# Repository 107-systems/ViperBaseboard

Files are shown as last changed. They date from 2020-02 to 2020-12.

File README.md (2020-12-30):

ViperBaseboard
==============

<p align="center">
  
</p>

This repository contains the requirements and the hardware design for MKR Vidor 4000 based Viper quadcopter.

## Quadcopter renderings
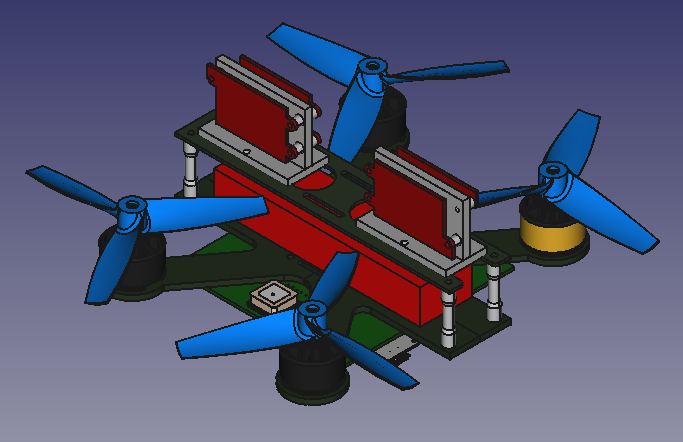
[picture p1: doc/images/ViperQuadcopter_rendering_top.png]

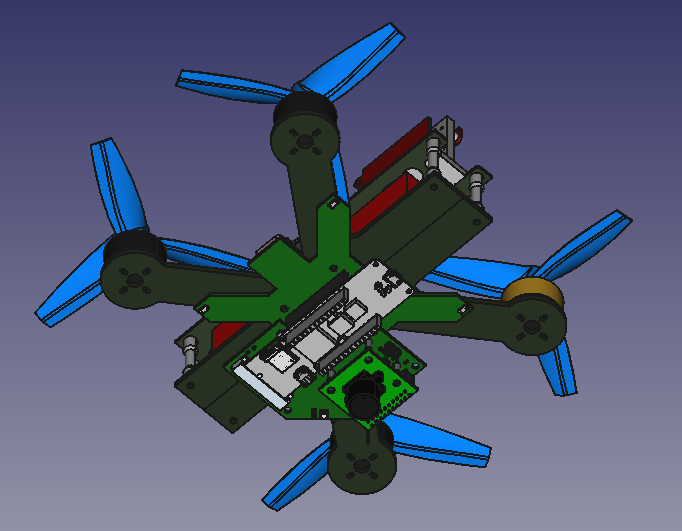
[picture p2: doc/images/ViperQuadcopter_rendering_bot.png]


## PCB renderings
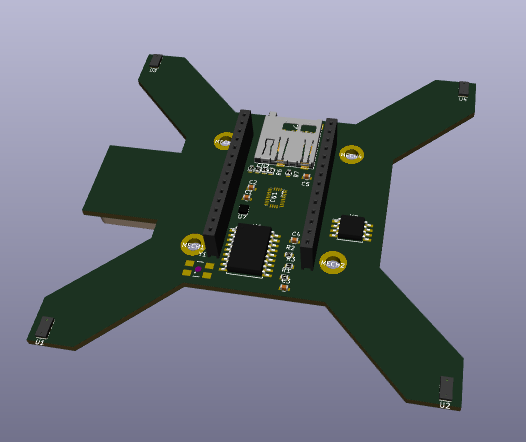
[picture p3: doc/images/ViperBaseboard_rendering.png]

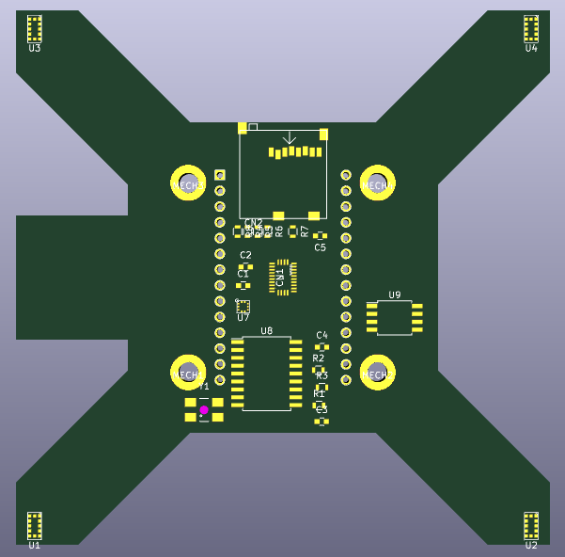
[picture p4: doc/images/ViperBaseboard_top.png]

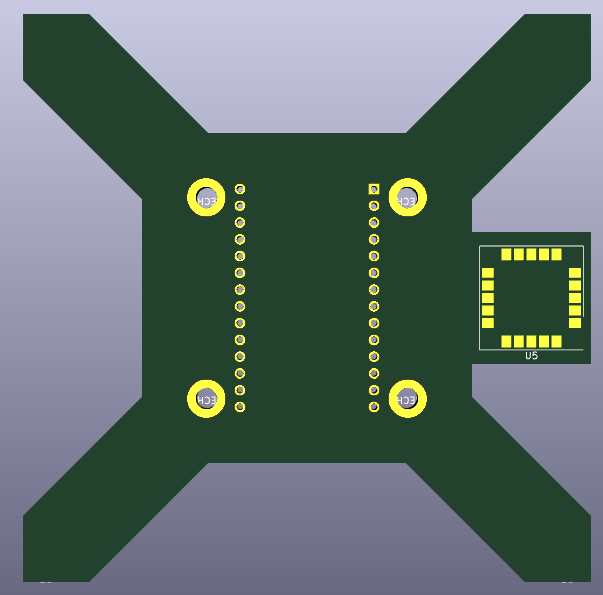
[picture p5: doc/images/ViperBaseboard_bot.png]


The **Viper Baseboard** serves as an adapter board between an Arduino MKR Vidor 4000 and various sensors and actuators in order to implement a flight controller for a quadcopter UAV.

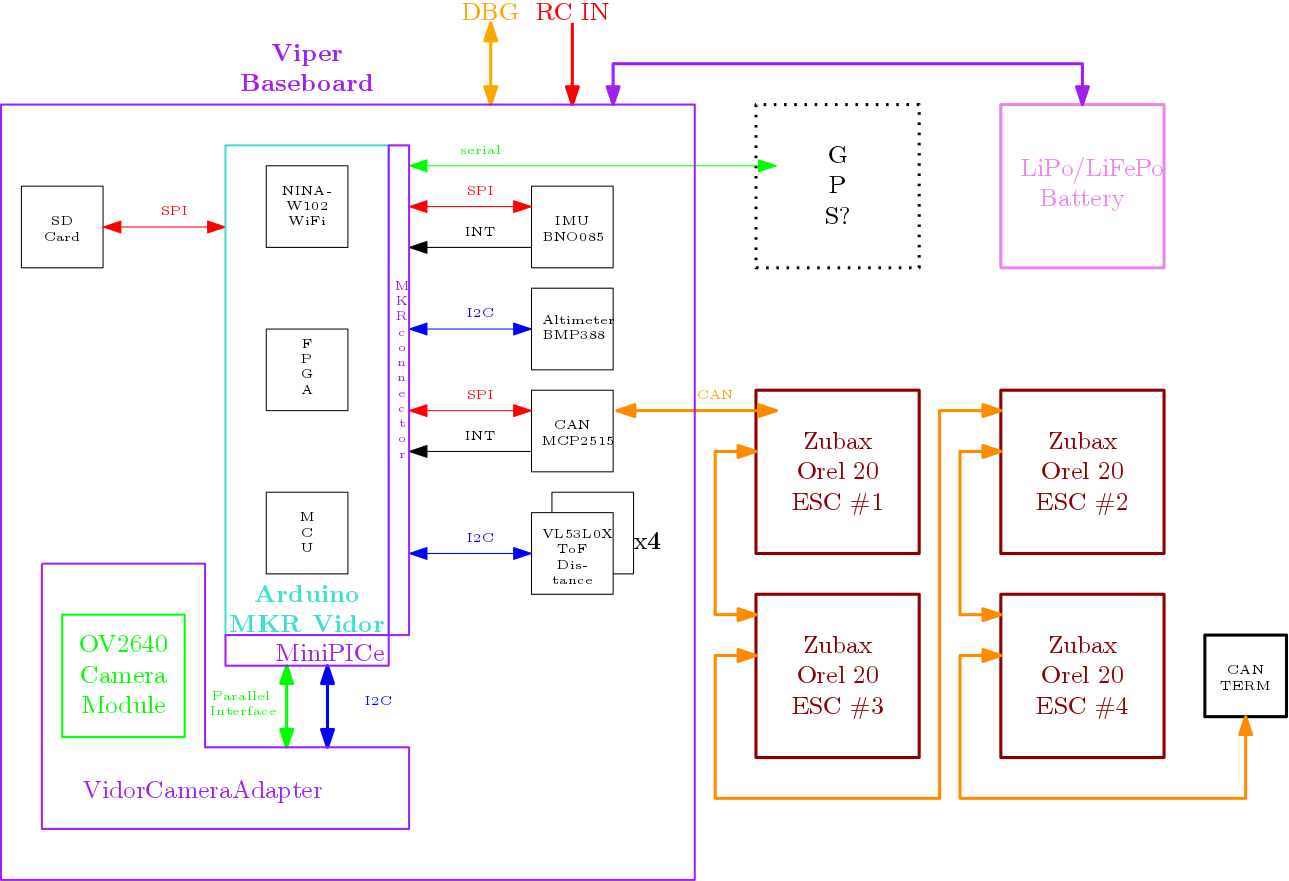
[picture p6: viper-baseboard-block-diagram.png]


The block diagramm has been created using [Ipe](http://ipe.otfried.org/) which can be installed via `sudo apt-get install ipe texlive-full` or `sudo apt-get install ipe texlive-base texlive-latex-recommended` for minimal installation).

## Requirements
### Functional Requirements
#### Rotational/Translational Stabilisation
The quadcopter should be able to stabilise itself against external disturbances concerning its orientation and position with respect to a given setpoint. For determining the current orientation of the quadcopter a suitable Inertial Measurement Unit (IMU) with a suitable sensor fusion algorithm shall be used. For determining translational stabilisation a optical flow sensor consisting of a downward facing camera in combination with a suitable optical flow sensor algorithm shall be used.

#### Vertical (Height) Stabilisation
The quadcopter should be able to hold a set distance over ground. In close proximity to the ground VL53L0X ToF sensors are used to  determine the distance between ground and quadcopter and prevent an accidential crash. When the distance between quadcopter and ground exceeds the maximum measurement range of the ground sensors the height will be controlled using a digital altimeter such as the BMP388.

#### WiFi based Control/Configuration
The quadcopter shall provide a WiFi access point to which a WiFi capable device can connect. Once a WiFi connection is established the quadcopter can be controlled via commands exchanged between quadcopter and device via a network socket. A webserver will run on the quadcopter which allows the user to configure and tweak certain aspects of the quadcopter configuration (e.g. control parameters) or read out quadcopter status.

#### Automonous Landing
The quadcopter should be able to land without user control. Three VL53L0X ToF sensors arranged in a triangle are used to determine the distance between ground and quadcopter and also perform an estimation of the grounds surface.

#### FPV (First-Person-View) Control
The image stream of a forward facing camera (a MIPI connector intented for use with the Omnivision OV5647 camera is available on the MKR VIDOR 4000 board) should be suitably encoded (in the FPGA) and transmitted via WiFi module in such way that a user can be view the image stream e.g. on a mobile phone which allows a FPV control of the quadcopter.\
It should be posible to switch the FPV from forward facing camera to ground facing camera and back. Then the user can choose which camera fits best his needs.

#### SD Card Storage
There should be a socket for a SD card on the baseboard. The flight controller then can log information like position or altitude or store video clips of the cameras or do image generation like map creation with the ground facing camera.

### Sensors
#### VL53L0X
The VL53L0X ToF Sensor allows a measurement range of up to 2 m with a resolution of 1 mm.\
**Attention:** all VL53L0X come up with the same I2C address. So we need additional circuitry to disable them with the XSHUT pin und give them individual addresses one after another.
#### BMP388
The BMP388 is a precision barometric pressure sensor wich relative accuracy of 8 Pascals, which translates to about ± 0.5 meter of altitude.
#### BNO085
The BNO085 contains 3 axis accelerometers, gyroscopes and magnetometers incl. onboard-algorithms for sensor fusion.
#### CD-PA1010D (Optional)
The [CD-PA1010D](doc/datasheet/Sensor-GPS-CD-PA1010D-v-0-3.pdf) is global positioning sensor supporting GPS, GLONASS, GALILEO, QZSS which can be interfaced both via UART and I2C.

### Actuators
#### Zubax Orel 20 ESCs
[Zubax Orel 20](https://kb.zubax.com/display/MAINKB/Zubax+Orel+20) are used as ESC (Electronic Speed Controllers) and controlled via [UAVCAN](https://uavcan.org).

### Electrical Requirements

* **Input Voltage**: 9 - 18.5 V (same as the Zubax Orel 20).
* **Input Protection**: Input voltage should be protected by a TVS diode against voltage spikes from the motors.
There is no fuse because the motor drivers can draw excessive currents. Then a fuse is useless because it should have a very high current rating and then it can'tprotect very much. Additionally the fuse would add additional weight and empose a risk of failure during flight.

#### Power planes and distribution
* **Input Voltage**: to motor drivers and input for voltage regulators, current: 20 to 30 A.
* **5V**:
Input for Arduino because the Arduino doesn't like to be directly fed with 3.3V.
generated on by a switching regulator.
Current: 500 mA + Current for 3.3V devices
* **3.3V**:
for sensors and camera module
generated by the onboard regulator of the Arduino
Current: up to 100 mA, should be OK for the onboard regulator

#### Connectors (mechanical and pinout)
##### Battery / Input
##### CAN
The Zubax Orel 20 ESCs utilize the [JST GH](http://www.jst-mfg.com/product/detail_e.php?series=105) connectors with a pitch of 1.25 mm.

| **Pin** | **Signal** |
|:---:|:---:|
| 1 | VCC |
| 2 | CAN_H |
| 3 | CAN_L |
| 4 | GND |

#### Connections of Arduino MKR Vidor 4000

* **MKR connector** (2.54 mm pinheader, 28 pins)
  * I2C
  * CAN over SPI (like on MKRCANShield)
  * 5V input, 3.3V output
  * RC_IN (for additional remote control receiver)

| **Pin** | **Pin Name** | **Signal** | **Description** |
|:---:|:---:|:---:|:---:|
| 1 | AREF | not connected | |
| 2 | DAC0/A0 | | |
| 3 | A1 | | |
| 4 | A2 | | |
| 5 | A3 | | |
| 6 | A4 | | |
| 7 | A5 | | |
| 8 | A6 | | |
| 9 | D0 | RC_IN | remote receiver input |
| 10 | D1 | | |
| 11 | D2 | | |
| 12 | D3 | MCP2515_CS | like MKRCANShield |
| 13 | D4 | SD_CS | like MKR SD PROTO SHIELD |
| 14 | D5 | | |
| 15 | D6 | | |
| 16 | D7 | MCP2515_INT | like MKRCANShield |
| 17 | D8/MOSI | MOSI | MCP2515 |
| 18 | D9/SCK | SCK | MCP2515 |
| 19 | D10/MISO | MISO | MCP2515 |
| 20 | D11/SDA | SDA | I2C for sensors |
| 21 | D12/SCL | SCL | I2C for sensors |
| 22 | D13/RX | GPS_RX | communication with gps module  |
| 23 | D14/TX | GPS_TX | communication with gps module  |
| 24 | RESET | not connected | |
| 25 | GND | GND | |
| 26 | 3V3 | 3V3-rail | supply voltage for sensors ... |
| 27 | VIN | 5V | input from voltage regulator |
| 28 | 5V | not connected | |

* **USB**: Programming and debugging
* **I2C**: Not used, redundant to MKR connector
* **LiPo**: not used, not suitable
* **MicroHDMI**: not used
* **MiPi Camera Connector**: reserved for front facing camera
* **MiniPCIe Connector**: Connection to OV2640 camera module serving as optical flow sensor. Using VidorCameraAdapter.

### Mechanical Requirements

* **Mounting**: No enclosure planed.
* **Mounting**: There should be mounting holes to mount the baseboard on the [Armattan F1-4B 3MM frame](https://www.armattanquads.com/f1-4b-3mm/)
* **Weight**: The weight should be as low as possible to get better flight performance
* **Cameras**: One camera is mounted on the botom and is facing to the ground. There is an option for a second camera facing forward.

### Environmental Requirements

* **Temperature**: Commercial temperature range should be OK. But parts with industrial range are preferred because of higher reliability.
* **Shock/Vibration**: Care should be taken because of higher vibration on copter therefore no high parts like electrolytic capacitors

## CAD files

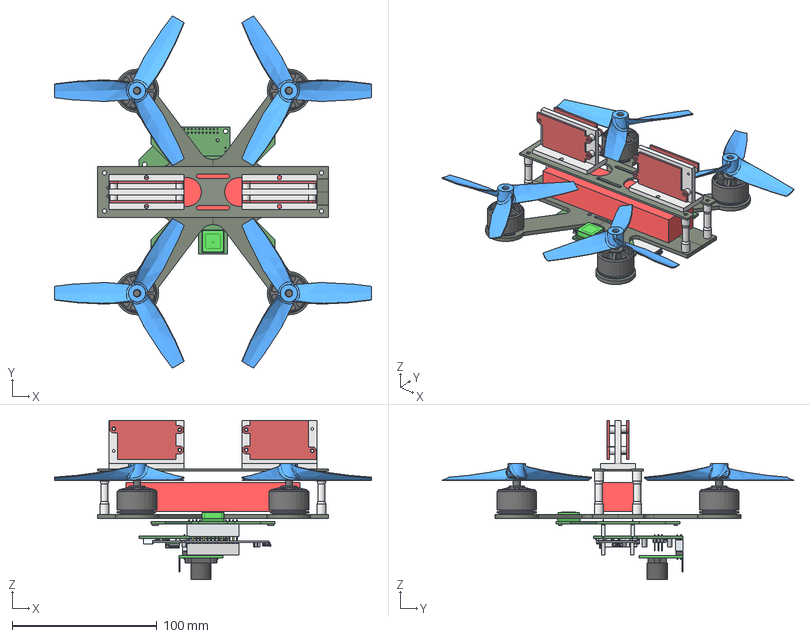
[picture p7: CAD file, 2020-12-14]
ViperQuadcopter.FCStd
219.3 x 243.4 x 110.2 mm
Frame_175mm
vidor
PCB
Package
X2
Pads
LILY_Antenna_Rev_D
685119248223_PIN
685119248223_PIN001
685119248223_PIN002
685119248223_PIN003
685119248223_PIN004
685119248223_PIN005
685119248223_PIN006
685119248223_PIN007
685119248223_PIN008
685119248223_INF
685119248223_SHIELDING
Shielding
Insulator
Pin
Pin001
Pin002
Pin003
Pin004
_T1SSW-114-03-G-S
_P2SSW-114-03-G-S
_T1SSW-114-03-G-S001
_P2SSW-114-03-G-S001
PCB002
pin
connector_frame
camera
battery
top plate
distance bolt
distance bolt001
distance bolt002
distance bolt003
zubax_orel001
zubax_orel
holder
zubax_orel002
zubax_orel003
holder001
T345V1_PROP
T345V1_PROP (Mirror #3)
T345V1_PROP (Mirror #7)
T345V1_PROP (Mirror #5)
F60 2200KV v2 (Mirror #4)
F60 2200KV v2
F60 2200KV v2 (Mirror #8)
F60 2200KV v2 (Mirror #6)

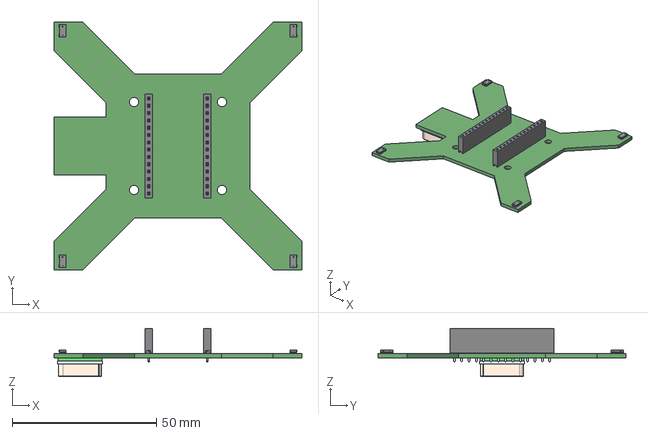
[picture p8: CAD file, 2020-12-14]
ViperBaseboard.step
86.0 x 86.0 x 16.7 mm

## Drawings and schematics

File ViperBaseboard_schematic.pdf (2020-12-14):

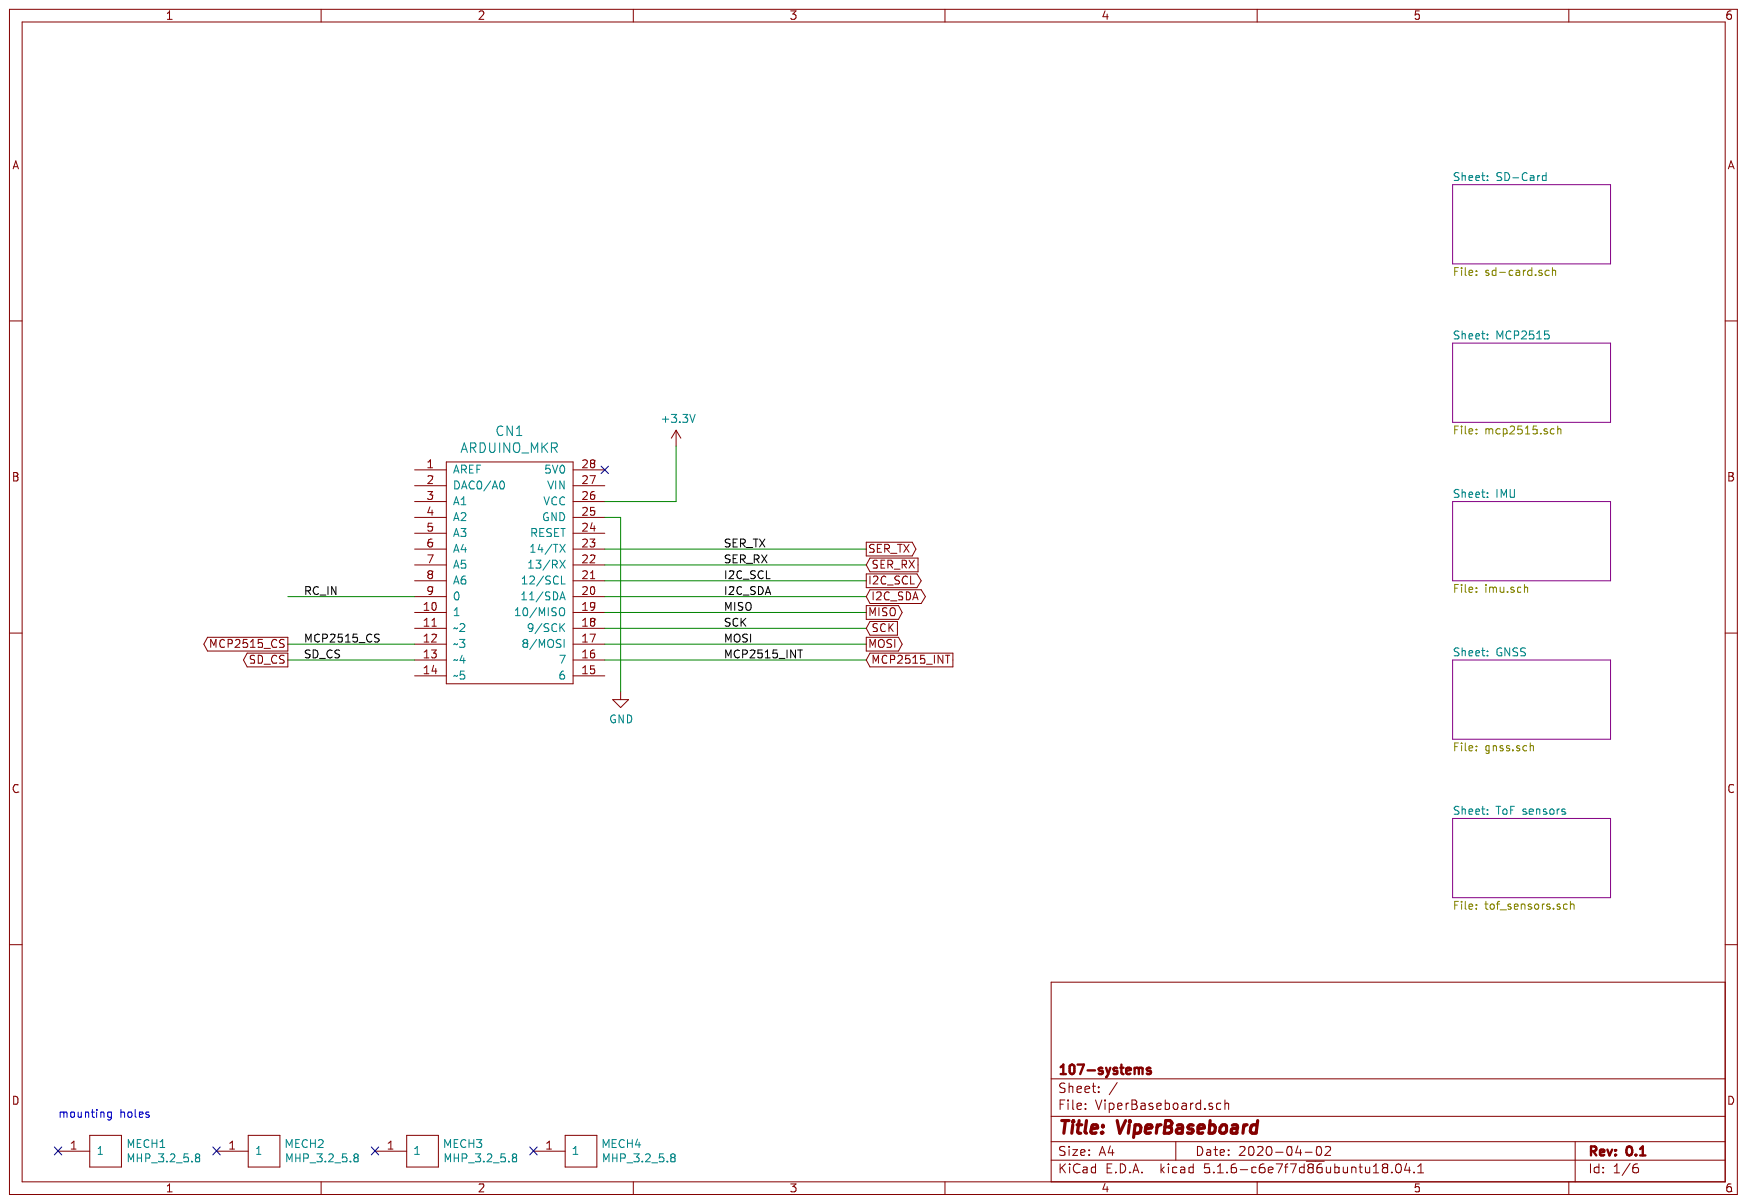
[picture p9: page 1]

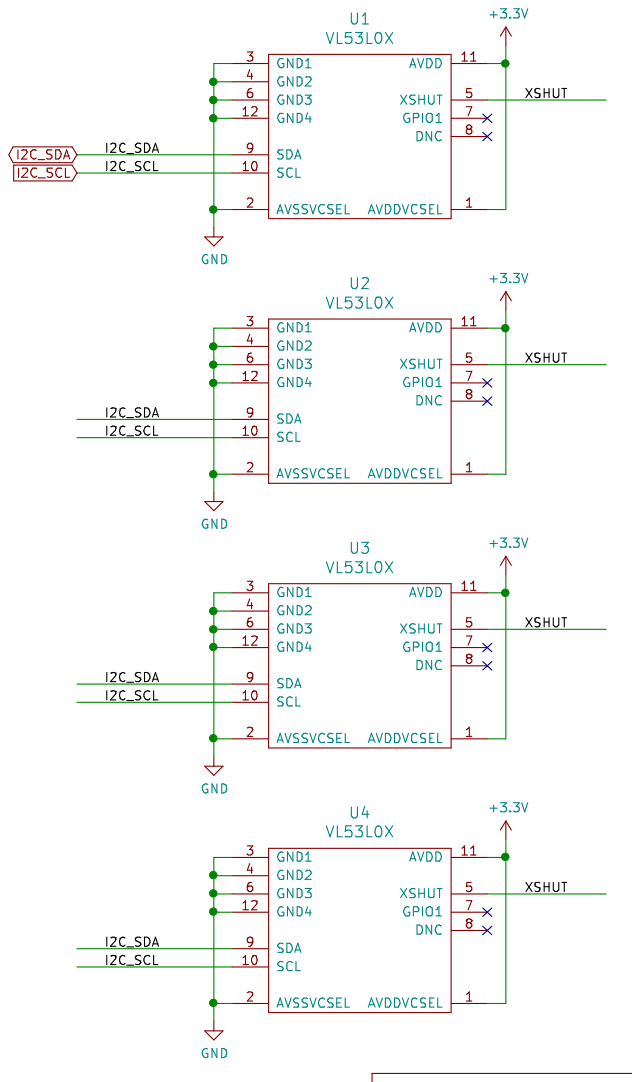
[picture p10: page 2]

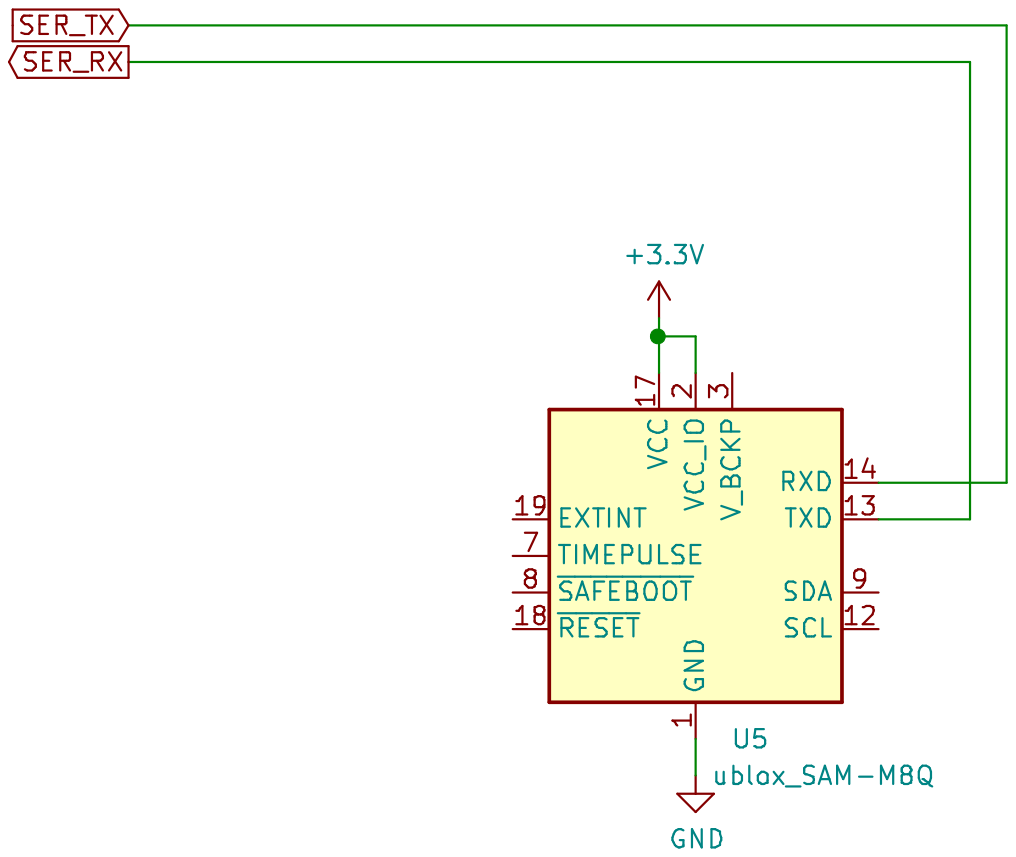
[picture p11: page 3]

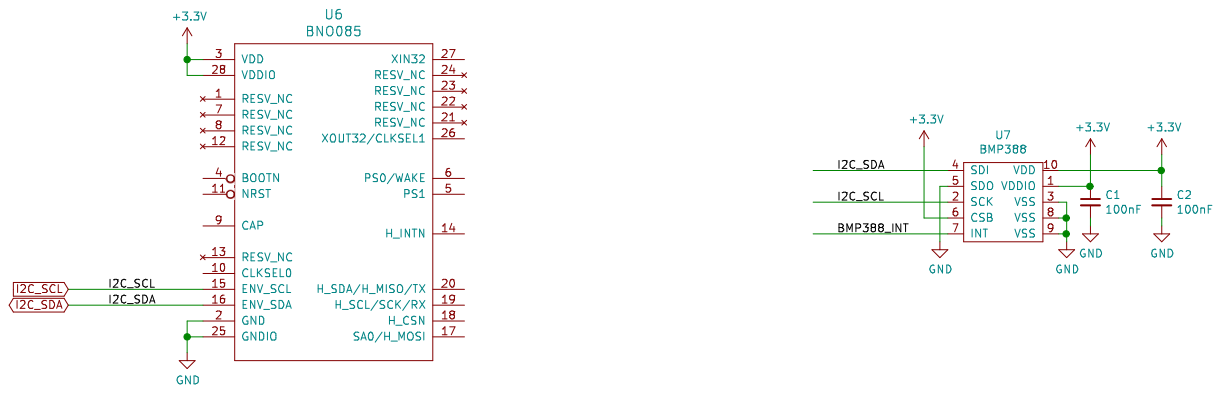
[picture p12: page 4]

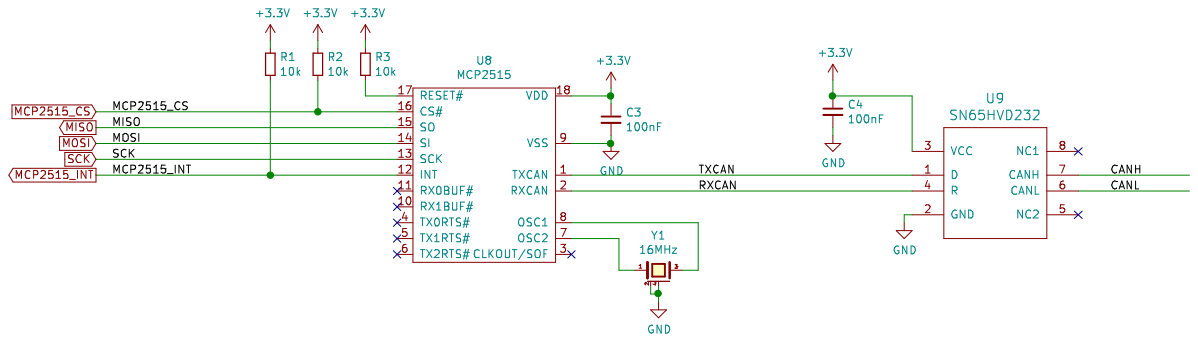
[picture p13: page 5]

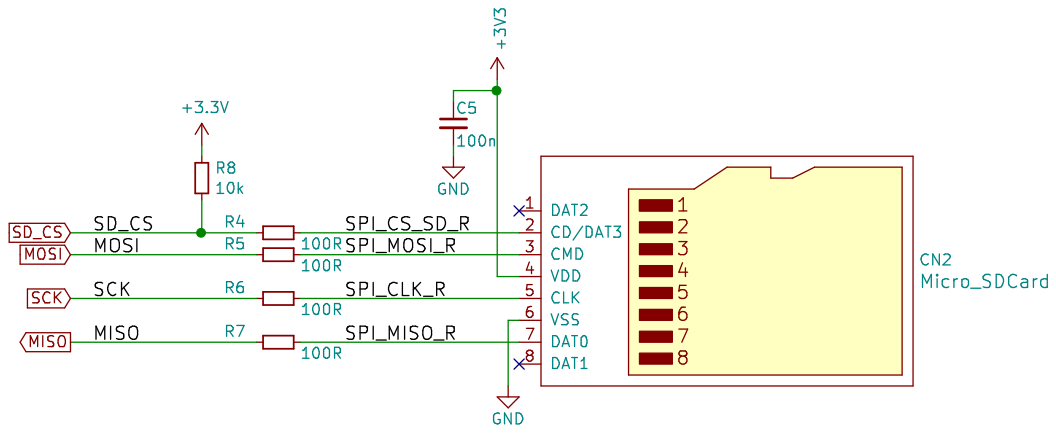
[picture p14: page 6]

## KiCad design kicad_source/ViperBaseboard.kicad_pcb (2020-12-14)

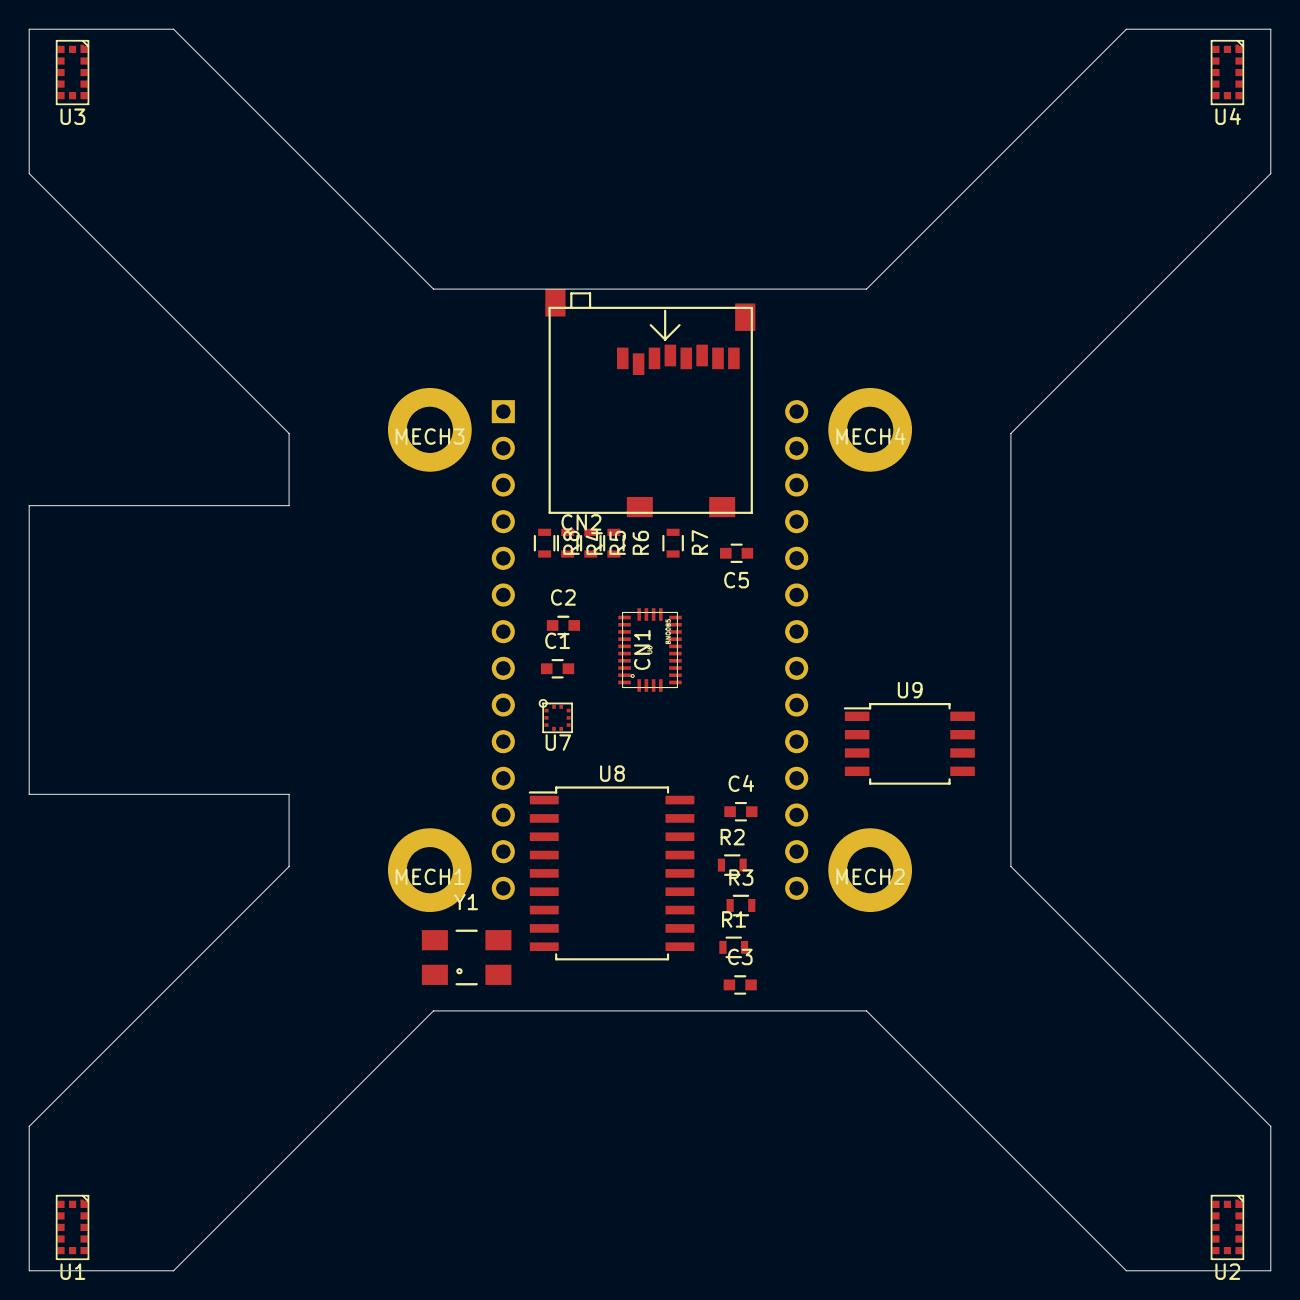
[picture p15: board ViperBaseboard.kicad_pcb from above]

Board: 2 copper layers, 86.0 x 86.0 mm, 29 parts (1 on the bottom side), 22 nets, no tracks yet.

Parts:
C1, C2, C3, C4: 100nF; C_0603
C5: 100n; C_0603
CN1: ARDUINO_MKR; ARDUINO_MKR_BASEBOARD
CN2: Micro_SDCard; WE_693071010811
MECH1, MECH2, MECH3, MECH4: MHP_3.2_5.8
R1, R2, R3, R8: 10k; R_0603
R4, R5, R6, R7: 100R; R_0603
U1, U2, U3, U4: VL53L0X
U5: ublox_SAM-M8Q
U6: BNO085; LGA-28-5832
U7: BMP388
U8: MCP2515; SOIC-18_7.5x11.6mm_Pitch1.27mm
U9: SN65HVD232; SOIJ-8_5.3x5.3mm_Pitch1.27mm
Y1: 16MHz; Crystal_SMD_0603_4Pads

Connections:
+3V3: C1.1, C2.1, C3.1, C4.1, C5.1, CN1.26, CN2.4, R1.1, R2.1, R3.1, R8.1, U1.1, U1.11, U2.1, U2.11, U3.1, U3.11, U4.1, U4.11, U5.2, U5.17, U6.3, U6.28, U7.1, U7.6, U7.10, U8.18, U9.3
/MCP2515/RXCAN: U8.2, U9.4
/MCP2515/TXCAN: U8.1, U9.1
/SD-Card/SPI_CLK_R: CN2.5, R6.1
/SD-Card/SPI_CS_SD_R: CN2.2, R4.1
/SD-Card/SPI_MISO_R: CN2.7, R7.1
/SD-Card/SPI_MOSI_R: CN2.3, R5.1
/ToF sensors/XSHUT: U1.5, U2.5, U3.5, U4.5
GND: C1.2, C2.2, C3.2, C4.2, C5.2, CN1.25, CN2.6, U1.2, U1.3, U1.4, U1.6, U1.12, U2.2, U2.3, U2.4, U2.6, U2.12, U3.2, U3.3, U3.4, U3.6, U3.12, U4.2, U4.3, U4.4, U4.6, U4.12, U5.1, U5.4, U5.5, U5.6, U5.10, U5.11, U5.15, U5.16, U5.20, U6.2, U6.25, U7.3, U7.5, U7.8, U7.9, U8.9, U9.2, Y1.2, Y1.4
I2C_SCL: CN1.21, U1.10, U2.10, U3.10, U4.10, U6.15, U7.2
I2C_SDA: CN1.20, U1.9, U2.9, U3.9, U4.9, U6.16, U7.4
MCP2515_CS: CN1.12, R2.2, U8.16
MCP2515_INT: CN1.16, R1.2, U8.12
MISO: CN1.19, R7.2, U8.15
MOSI: CN1.17, R5.2, U8.14
unnamed: R3.2, U8.17
unnamed: U8.7, Y1.1
unnamed: U8.8, Y1.3
SCK: CN1.18, R6.2, U8.13
SD_CS: CN1.13, R4.2, R8.2
SER_RX: CN1.22, U5.13
SER_TX: CN1.23, U5.14

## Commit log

2020-02-12 Requirements for Viper Baseboard (#1)
    * Creating initial block diagram of viper base board
    * Adding block diagram to README.
    * Specify BMP388 as altimeter and BNO085 as IMU, also adding debug and RC PWM inputs
    * Removing PWR block since the need for a power unit for the adapter board is quite obvious
    * Adding requirement for autonomous landing
    * added mechanical, electrical and environmental requirements
    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
2020-04-02 CD PA1010D as GPS sensor (#2)
    * Adding suggestion of CD PA1010D GPS sensor to requirements
    * Added 3D model and rendering of ViperQuadcopter
    * Added image of rendering of quadcopter
    * Started pcb schematic and layout
    * Updated layout, added step of baseboard
    * Updated 3d model of viperquadcopter with baseboard, generated some screenshots
    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
    [ViperBaseboard.kicad_pcb, ViperBaseboard.sch, ViperBaseboard.step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]
2020-04-03 corrected frame size of quadcopter
    [ViperQuadcopter.FCStd]
2020-04-13 updated 3D model with correct dimensions of F1-4B frame
    [ViperQuadcopter.FCStd]
2020-04-13 added motor drivers, props and motors to 3d model
    [ViperQuadcopter.FCStd]
2020-04-25 redefined shape of PCB
    [ViperBaseboard.kicad_pcb, ViperBaseboard.sch, ViperBaseboard.step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]
2020-06-03 added BMP388
    [ViperBaseboard.kicad_pcb, imu.sch]
2020-06-03 added schematic sheet with MCP2515
    [ViperBaseboard.kicad_pcb, ViperBaseboard.sch, gnss.sch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]
2020-06-03 added schematic sheet with sd-card
    [ViperBaseboard.kicad_pcb, ViperBaseboard.sch, gnss.sch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]
2020-06-03 added renderings of pcb
